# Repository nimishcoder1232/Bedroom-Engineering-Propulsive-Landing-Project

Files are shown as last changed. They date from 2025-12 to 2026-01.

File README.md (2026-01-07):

# Bedroom-Engineering-Propulsive-Landing-Project
This repo has everything that I made for my rocket that can propulsive landing, while still being under ITAR restrictions. 

For this project, I will design a rocket that can launch and then do a propulsive landing. In order to meet this challenge, I will have to make a new custom ESP32-based flight computer. I will have to make a quaternion orientation calculation system, I will have to design a control loop, and I will have to make a simulator in Python, without vibe coding, because it is too complicated. The simulator will simulate the rocket’s flight to help tune the control loop and the propulsive landing.

I did this project for a few reasons. The first reason I did it, is because in gneral, this is my passion. I love both engineering and rockets, so this is satisfactory for me. This isant a project for me, this project is more, who I am. I also made this project to learn from it. Throughout this project, I have learned sooo much, PCB design, CAD, Programign in many languages, soldering. And SO much more. Every time I sit down to do one of these projects, I end up learning so much. That is the second reason I work on these projects, To learn From them. 

Notes:
I am 3d printing everything myself, I DONT need reinbursment

The cad has all the parts. The engine, and the dc motor, and the syringes, are provided by me. 

The cad is ONE zip file. Once you unpack it, it has ALL the parts. the file in ALL CAPS called FULL ASEMBLY is the completed asembbly. 

No explosives are in any of the BOM, no engines, nothing. 

Project Link: https://blueprint.hackclub.com/projects/7459

Full Rocket: 



PCB schematic: 



PCB Routing: 



PCB Preview: 



Wiring Diagram: 

Any bold line is a electrical wire. I have color coded it. black for ground, red for power, and blue for saignals. if two same color lines touch, thats a connection, if two ddifferent colored lines overlaped, thats NOT a connection. 


|Item Name |Link |Quanity|Cost  USD|Notes |
|---|---|---|---|---|
|Carbon Fiber Rod 500mm 5 pack |https://www.aliexpress.com/item/3256806607506929.html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 |2 |9 | |
|drv8833 motor controler 1 pack |https://www.aliexpress.com/item/3256809542138701.html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 |1 |5 | |
|ES08MA &#124;&#124; servos 2 poack |https://www.aliexpress.com/item/3256809559338882.html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|1 |15 | |
|Solder Paste |https://www.aliexpress.com/item/3256804805080766.html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 |1 |7.11 | |
|Taxes deducted from Ali Express |N.A. |1 |4 | |
| | | | | |
|USB4105-GF-A |https://www.digikey.com/en/products/detail/gct/USB4105-GF-A/11198441 |2 |1.56 |Some of these components, I ordered extra because its LITTERLY cheaper to buy more|
|CP2102N-A02-GQFN28R |https://www.digikey.com/en/products/detail/silicon-labs/CP2102N-A02-GQFN28R/9863480 |2 |8.64 | |
|BMI270 |https://www.digikey.com/en/products/detail/bosch-sensortec/BMI270/9974486 |2 |7.46 | |
|BMP390 |https://www.digikey.com/en/products/detail/bosch-sensortec/BMP390/16164575 |2 |6.3 | |
|MMBT4401_R1_00001 |https://www.digikey.com/en/products/detail/panjit-international-inc/MMBT4401-R1-00001/14661149 |4 |0.64 | |
|OSTTE020104 |https://www.digikey.com/en/products/detail/on-shore-technology-inc/OSTTE020104/2351816 |10 |3.61 | |
|PS1240P02BT |https://www.digikey.com/en/products/detail/tdk-corporation/PS1240P02BT/935924 |2 |1.24 | |
|CL21B106KOQNNNE |https://www.digikey.com/en/products/detail/samsung-electro-mechanics/CL21B106KOQNNNE/3888530 |15 |0.53 | |
|C0805C104K5RACTU |https://www.digikey.com/en/products/detail/kemet/C0805C104K5RACTU/411169 |20 |0.32 | |
|B320A-13-F |https://www.digikey.com/en/products/detail/diodes-incorporated/B320A-13-F/717692 |6 |1.56 | |
|ESD5Z5.0T5G |https://www.digikey.com/en/products/detail/onsemi/ESD5Z5-0T5G/5404303 |10 |0.99 | |
|TPS565208DDCR |https://www.digikey.com/en/products/detail/texas-instruments/TPS565208DDCR/7776393 |2 |2.76 | |
|LD1117S33TR |https://www.digikey.com/en/products/detail/stmicroelectronics/LD1117S33TR/585766 |2 |0.68 | |
|ESP32-S3-WROOM-1-N8 |https://www.digikey.com/en/products/detail/espressif-systems/ESP32-S3-WROOM-1-N8/15200089 |2 |10.98 | |
|CL21B105KBFNNNE |https://www.digikey.com/en/products/detail/samsung-electro-mechanics/CL21B105KBFNNNE/3886687 |10 |0.13 | |
|CL21A226MAYNNNE |https://www.digikey.com/en/products/detail/samsung-electro-mechanics/CL21A226MAYNNNE/10479857 |3 |0.24 | |
|LTST-C170GKT |https://www.digikey.com/en/products/detail/liteon/LTST-C170GKT/269226 |3 |0.3 | |
|AO3400A |https://www.digikey.com/en/products/detail/alpha-omega-semiconductor-inc/AO3400A/1855772 |10 |2.82 | |
|MLZ2012P220WT000 |https://www.digikey.com/en/products/detail/tdk-corporation/MLZ2012P220WT000/4327893 |2 |0.2 | |
|CRCW08051K00FKEA |https://www.digikey.com/en/products/detail/vishay-dale/CRCW08051K00FKEA/1175637 |2 |0.2 | |
|RMCF0805FT22K1 |https://www.digikey.com/en/products/detail/stackpole-electronics-inc/RMCF0805FT22K1/1760211 |10 |0.07 | |
|RMCF0805FT10K0 |https://www.digikey.com/en/products/detail/stackpole-electronics-inc/RMCF0805FT10K0/1760676 |16 |0.21 | |
|RC0805JR-075K1L |https://www.digikey.com/en/products/detail/yageo/RC0805JR-075K1L/728338 |10 |0.08 | |
|W25Q128JVSIM |https://www.digikey.com/en/products/detail/winbond-electronics/W25Q128JVSIM/6819721 |2 |3.94 | |
|RC0805FR-072K2L |https://www.digikey.com/en/products/detail/yageo/RC0805FR-072K2L/727676 |10 |0.1 | |
|RC0805FR-0747K5L |https://www.digikey.com/en/products/detail/yageo/RC0805FR-0747K5L/727975 |10 |0.1 | |
|RT0805BRD0759R7L |https://www.digikey.com/en/products/detail/yageo/RT0805BRD0759R7L/7708567 |2 |0.32 | |
|RC0805FR-07330RL |https://www.digikey.com/en/products/detail/yageo/RC0805FR-07330RL/727866 |10 |0.1 | |
|Dijikey Shipping |N.A. |1 |7 | |
|Sales tax + terrifs (Dijikey) |N.A. |1 |8 | |
| | | | | |
|JLCPCB 4 Layer PCB + stencil + Global Standard Dirrect Line + sales tax|JLC PCB |5 |33 | |
| | | | | |
|JLC PCB order |33 | | | |
| | | | | |
|Ali express order |40.11 | | | |
| | | | | |
|Dijikey Order |71.08 | | | |
| | | | | |
|Total Cost |144.19 | | | |

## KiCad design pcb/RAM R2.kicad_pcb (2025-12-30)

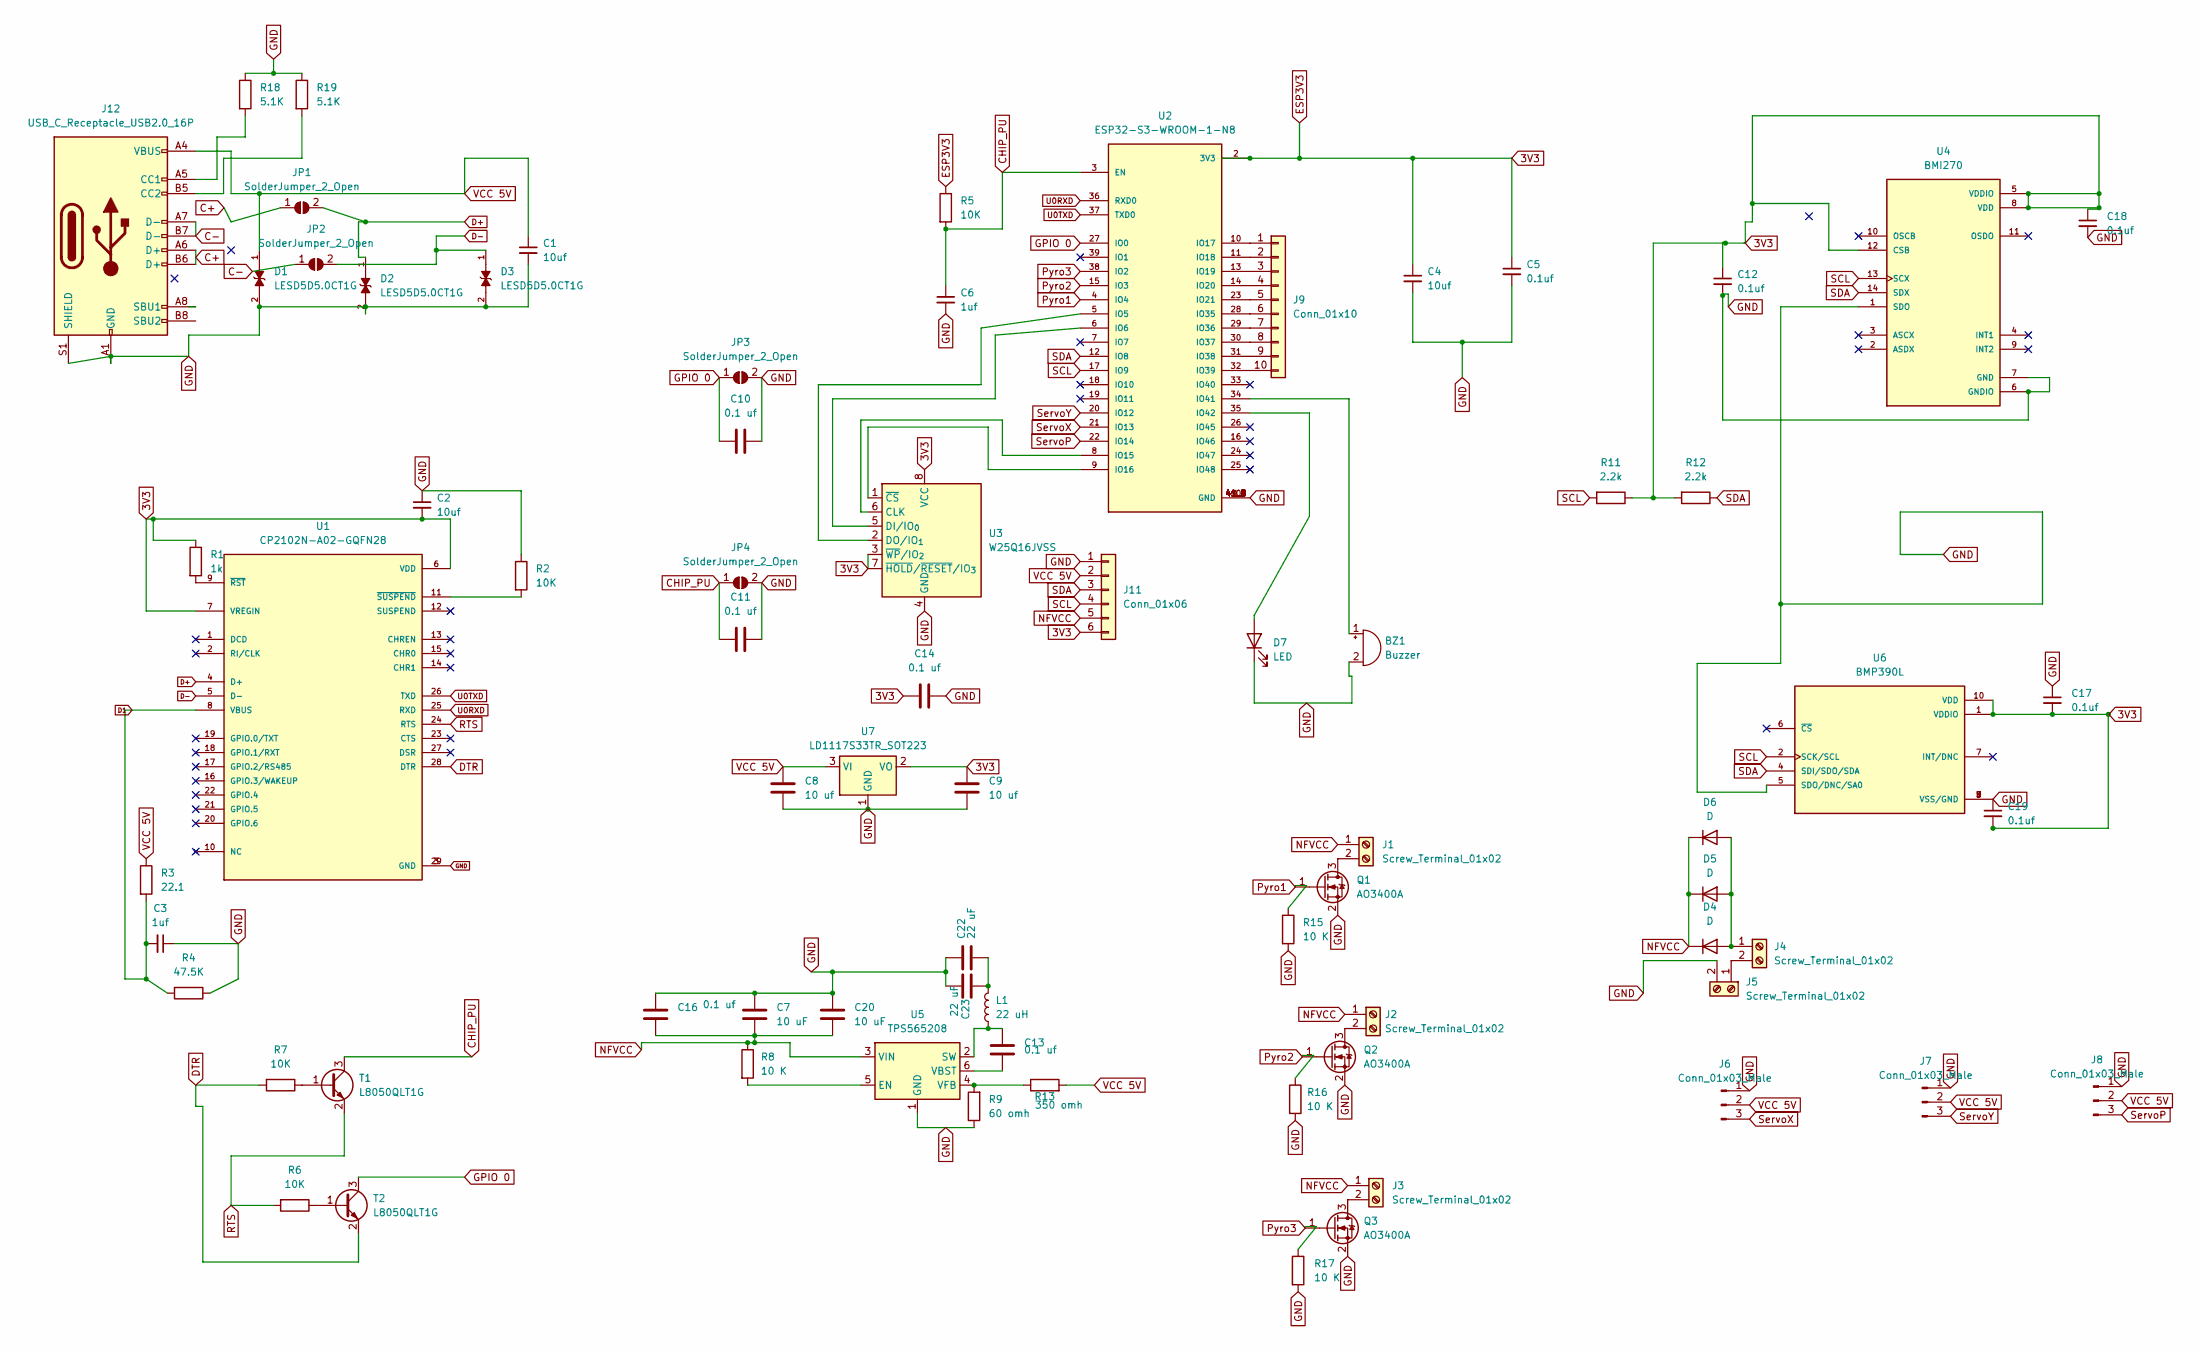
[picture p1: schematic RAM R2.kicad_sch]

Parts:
BZ1: Buzzer; Buzzer_TDK_PS1240P02BT_D12.2mm_H6.5mm
C1, C2, C4: 10uf; C_0805_2012Metric
C3, C6: 1uf; C_0805_2012Metric
C5, C12, C17, C18, C19: 0.1uf; C_0805_2012Metric
C7, C20: 10 uF; C_0805_2012Metric
C8, C9: 10 uf; C_0805_2012Metric
C10, C11, C13, C14, C16: 0.1 uf; C_0805_2012Metric
C22, C23: 22 uF; C_0805_2012Metric
D1, D2, D3: LESD5D5.0CT1G; TVS_LESD5D5.0CT1G; PARTREV O
D4, D5, D6: D; D_SMA
D7: LED; LED_0805_2012Metric
J1, J2, J3, J4, J5: Screw_Terminal_01x02; TerminalBlock_4Ucon_1x02_P3.50mm_Horizontal
J6, J7, J8: Conn_01x03_Male; PinHeader_1x03_P2.54mm_Vertical
J9: Conn_01x10; 10 pad genaric
J11: Conn_01x06; 6pad genaric
J12: USB_C_Receptacle_USB2.0_16P; USB_C_Receptacle_GCT_USB4105-xx-A_16P_TopMnt_Horizontal
JP1, JP2, JP3, JP4: SolderJumper_2_Open; SolderJumper-2_P1.3mm_Open_Pad1.0x1.5mm
L1: 22 uH; L_0805_2012Metric
Q1, Q2, Q3: AO3400A; SOT-23
R1: 1k; R_0805_2012Metric
R2, R5, R6, R7: 10K; R_0805_2012Metric
R3: 22.1; R_0805_2012Metric
R4: 47.5K; R_0805_2012Metric
R8, R15, R16, R17: 10 K; R_0805_2012Metric
R9: 60 omh; R_0805_2012Metric
R11, R12: 2.2k; R_0805_2012Metric
R13: 350 omh; R_0805_2012Metric
R18, R19: 5.1K; R_0805_2012Metric
T1, T2: L8050QLT1G; SOT-23
U1: CP2102N-A02-GQFN28; QFN50P500X500X80-29N; PARTREV 1.5
U2: ESP32-S3-WROOM-1-N8; XCVR_ESP32-S3-WROOM-1-N8
U3: W25Q16JVSS; SOIC-8_5.3x5.3mm_P1.27mm
U4: BMI270; XDCR_BMI270
U5: TPS565208; SOT-23-6
U6: BMP390L; XDCR_BMP390L; PARTREV 1.7
U7: LD1117S33TR_SOT223; SOT-223-3_TabPin2

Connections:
3V3: C2.2, C4.1, C5.1, C9.1, C12.1, C14.2, C17.2, C18.1, C19.2, J11.6, R1.1, R5.1, R11.1, R12.2, U1.6 (VDD), U1.7 (VREGIN), U2.2 (3V3), U3.3 (~WP/IO_{2}), U3.7 (~HOLD/~RESET/IO_{3}), U3.8 (VCC), U4.5 (VDDIO), U4.8 (VDD), U4.12 (CSB), U6.1 (VDDIO), U6.10 (VDD), U7.2 (VO)
C+: J12.A6 (D+), J12.B6 (D+), JP1.1 (A)
C-: J12.A7 (D-), J12.B7 (D-), JP2.1 (A)
CHIP_PU: C6.1, C11.2, JP4.1 (A), R5.2, T1.3 (C), U2.3 (EN)
D1: C3.2, R3.2, R4.2, U1.8 (VBUS)
D+: D2.1, JP1.2 (B), U1.4 (D+)
D-: D3.1, JP2.2 (B), U1.5 (D-)
DTR: R7.2, T2.2 (E), U1.28 (DTR)
GND: BZ1.2 (+), C1.2, C2.1, C3.1, C4.2, C5.2, C6.2, C7.1, C8.2, C9.2, C10.1, C11.1, C12.2, C14.1, C16.1, C17.1, C18.2, C19.1, C20.1, C22.1, C23.1, D1.2, D2.2, D3.2, D7.1 (K), J5.2, J6.1, J7.1, J8.1, J11.1, J12.A1 (GND), J12.A12 (GND), J12.B1 (GND), J12.B12 (GND), J12.S1 (SHIELD), JP3.2 (B), JP4.2 (B), Q1.2 (S), Q2.2 (S), Q3.2 (S), R2.1, R4.1, R9.1, R15.2, R16.2, R17.2, R18.1, R19.1, U1.3 (GND), U1.29 (GND), U2.1 (GND), U2.40 (GND), U2.41_1 (GND), U2.41_2 (GND), U2.41_3 (GND), U2.41_4 (GND), U2.41_5 (GND), U2.41_6 (GND), U2.41_7 (GND), U2.41_8 (GND), U2.41_9 (GND), U3.4 (GND), U4.1 (SDO), U4.6 (GNDIO), U4.7 (GND), U5.1 (GND), U6.3 (VSS/GND), U6.5 (SDO/DNC/SA0), U6.8 (VSS/GND), U6.9 (VSS/GND), U7.1 (GND)
GPIO 0: C10.2, JP3.1 (A), T2.3 (C), U2.27 (IO0)
NFVCC: C7.2, C16.2, C20.2, D4.1 (K), D5.1 (K), D6.1 (K), J1.1, J2.1, J3.1, J11.5, R8.1, U5.3 (VIN)
unnamed: BZ1.1 (-), U2.34 (IO41)
unnamed: C22.2, C23.2, L1.2
unnamed: D4.2 (A), D5.2 (A), D6.2 (A), J4.1
unnamed: D7.2 (A), U2.35 (IO42)
unnamed: J1.2, Q1.3 (D)
unnamed: J2.2, Q2.3 (D)
unnamed: J3.2, Q3.3 (D)
unnamed: J4.2, J5.1
unnamed: J9.1, U2.10 (IO17)
unnamed: J9.2, U2.11 (IO18)
unnamed: J9.3, U2.13 (IO19)
unnamed: J9.4, U2.14 (IO20)
unnamed: J9.5, U2.23 (IO21)
unnamed: J9.6, U2.28 (IO35)
unnamed: J9.7, U2.29 (IO36)
unnamed: J9.8, U2.30 (IO37)
unnamed: J9.9, U2.31 (IO38)
unnamed: J9.10, U2.32 (IO39)
unnamed: J12.A5 (CC1), R18.2
unnamed: J12.B5 (CC2), R19.2
unnamed: R7.1, T1.1 (B)
unnamed: R6.1, T2.1 (B)
unnamed: R1.2, U1.9 (~RST)
unnamed: R2.2, U1.11 (~SUSPEND)
unnamed: U2.5 (IO5), U3.2 (DO/IO_{1})
unnamed: U2.6 (IO6), U3.5 (DI/IO_{0})
unnamed: U2.8 (IO15), U3.6 (CLK)
unnamed: U2.9 (IO16), U3.1 (~CS)
unnamed: R8.2, U5.5 (EN)
unnamed: C13.1, L1.1, U5.2 (SW)
unnamed: C13.2, U5.6 (VBST)
unnamed: R9.2, R13.1, U5.4 (VFB)
Pyro1: Q1.1 (G), R15.1, U2.4 (IO4)
Pyro2: Q2.1 (G), R16.1, U2.15 (IO3)
Pyro3: Q3.1 (G), R17.1, U2.38 (IO2)
RTS: R6.2, T1.2 (E), U1.24 (RTS)
SCL: J11.4, R11.2, U2.17 (IO9), U4.13 (SCX), U6.2 (SCK/SCL)
SDA: J11.3, R12.1, U2.12 (IO8), U4.14 (SDX), U6.4 (SDI/SDO/SDA)
ServoP: J8.3, U2.22 (IO14)
ServoX: J6.3, U2.21 (IO13)
ServoY: J7.3, U2.20 (IO12)
U0RXD: U1.25 (RXD), U2.36 (RXD0)
U0TXD: U1.26 (TXD), U2.37 (TXD0)
VCC 5V: C1.1, C8.1, D1.1, J6.2, J7.2, J8.2, J11.2, J12.A4 (VBUS), J12.A9 (VBUS), J12.B4 (VBUS), J12.B9 (VBUS), R3.1, R13.2, U7.3 (VI)

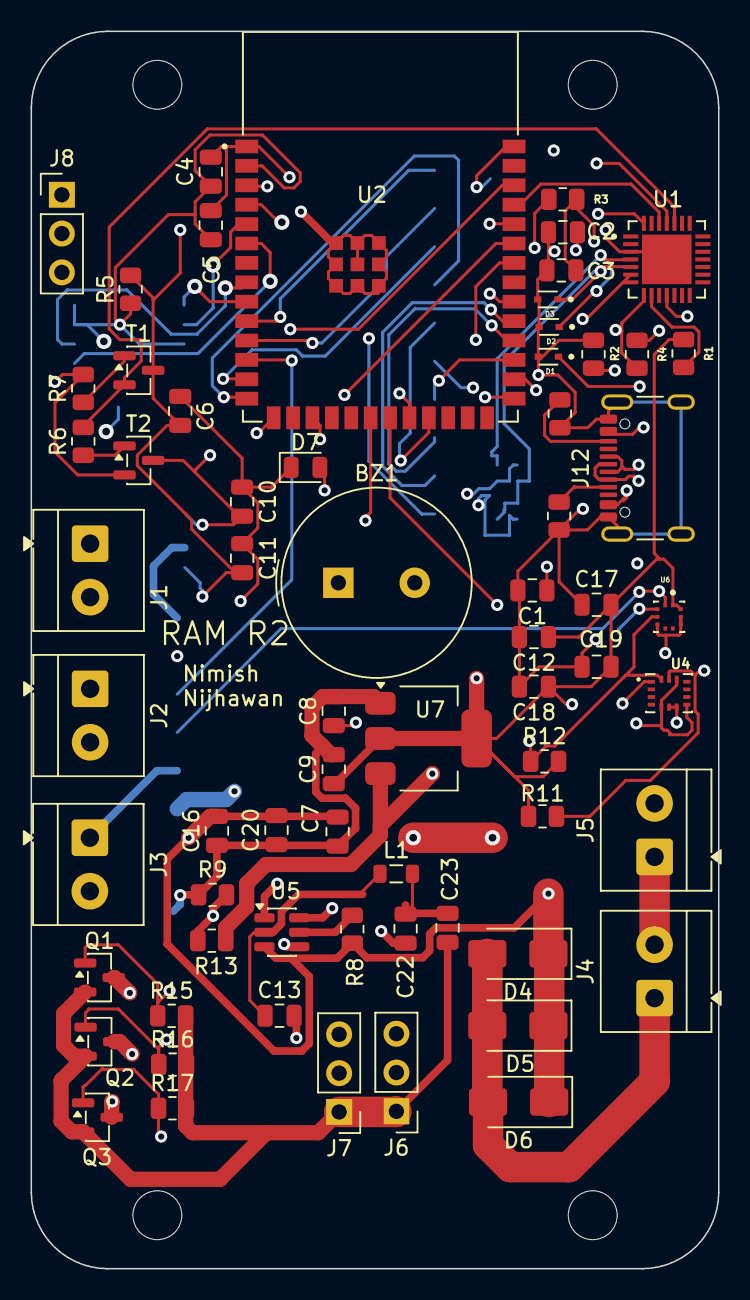
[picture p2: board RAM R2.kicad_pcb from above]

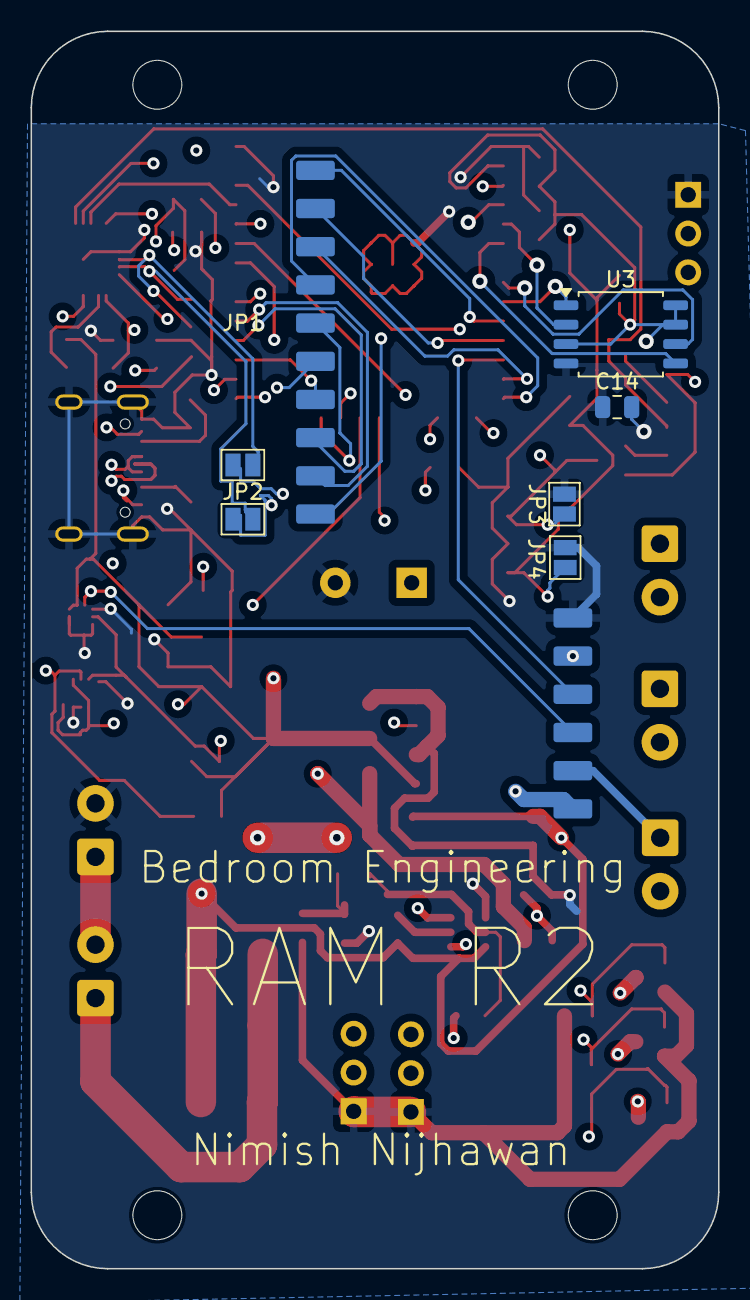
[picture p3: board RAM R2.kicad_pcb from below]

Board: 4 copper layers, 45.0 x 81.0 mm, 74 parts (8 on the bottom side), 55 nets.

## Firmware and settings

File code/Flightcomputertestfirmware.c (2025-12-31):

/*
This code tests the flight computer, and all of its functions, and proves capibilites liek PID. it DOES NOT have actual rocket guidence code, since that is ileagal.
A blueprint organizer has aproved, that I dont have to provide the guidence code in github. The real code DOES exist, but I cant share it.
*/

#include <Wire.h>
#include <ESP32Servo.h>
#include <Adafruit_BMP3XX.h>
#include "BMI270_SensorAPI.h"

// ================= PINS =================
#define SERVO_PIN 25
#define PYRO1_PIN 26
#define PYRO2_PIN 27

// ================= OBJECTS =================
Servo testServo;
Adafruit_BMP3XX bmp;

// BMI270 variables
struct bmi2_dev bmi;
struct bmi2_sens_data sensor_data;

// ================= PID =================
float targetAngle = 0.0;   // degrees
float angle = 0.0;
float gyroRate = 0.0;

float Kp = 3.0;
float Ki = 0.02;
float Kd = 0.15;

float error, lastError = 0;
float integral = 0;
float derivative;
float pidOutput;

// Timing
unsigned long lastTime;

// ================= BMI CALLBACKS =================
int8_t bmi_read(uint8_t reg, uint8_t *data, uint32_t len, void *intf_ptr) {
  Wire.beginTransmission(BMI2_I2C_PRIM_ADDR);
  Wire.write(reg);
  Wire.endTransmission(false);
  Wire.requestFrom(BMI2_I2C_PRIM_ADDR, len);
  for (uint32_t i = 0; i < len; i++) data[i] = Wire.read();
  return BMI2_OK;
}

int8_t bmi_write(uint8_t reg, const uint8_t *data, uint32_t len, void *intf_ptr) {
  Wire.beginTransmission(BMI2_I2C_PRIM_ADDR);
  Wire.write(reg);
  for (uint32_t i = 0; i < len; i++) Wire.write(data[i]);
  Wire.endTransmission();
  return BMI2_OK;
}

void bmi_delay(uint32_t ms, void *intf_ptr) {
  delay(ms);
}

// ================= SETUP =================
void setup() {
  Serial.begin(115200);
  Wire.begin();

  pinMode(PYRO1_PIN, OUTPUT);
  pinMode(PYRO2_PIN, OUTPUT);
  digitalWrite(PYRO1_PIN, LOW);
  digitalWrite(PYRO2_PIN, LOW);

  // Servo
  testServo.setPeriodHertz(50);
  testServo.attach(SERVO_PIN, 1000, 2000);

  // BMP390
  if (!bmp.begin_I2C()) {
    Serial.println("BMP390 FAIL");
    while (1);
  }

  bmp.setTemperatureOversampling(BMP3_OVERSAMPLING_8X);
  bmp.setPressureOversampling(BMP3_OVERSAMPLING_4X);
  bmp.setIIRFilterCoeff(BMP3_IIR_FILTER_COEFF_3);

  // BMI270
  bmi.intf = BMI2_I2C_INTF;
  bmi.read = bmi_read;
  bmi.write = bmi_write;
  bmi.delay_us = bmi_delay;
  bmi.intf_ptr = NULL;

  if (bmi270_init(&bmi) != BMI2_OK) {
    Serial.println("BMI270 FAIL");
    while (1);
  }

  bmi2_sens_config config[2];
  config[0].type = BMI2_ACCEL;
  config[1].type = BMI2_GYRO;

  bmi2_set_sensor_config(config, 2, &bmi);
  bmi2_sensor_enable(BMI2_ACCEL | BMI2_GYRO, &bmi);

  lastTime = millis();

  Serial.println("SYSTEM OK");
}

// ================= LOOP =================
void loop() {
  unsigned long now = millis();
  float dt = (now - lastTime) / 1000.0;
  lastTime = now;

  // ===== IMU =====
  bmi2_get_sensor_data(&sensor_data, &bmi);

  float ax = sensor_data.acc.x / 16384.0;
  float az = sensor_data.acc.z / 16384.0;
  gyroRate = sensor_data.gyr.y * 0.061; // deg/s

  float accelAngle = atan2(ax, az) * 57.2958;

  // Complementary filter
  angle = 0.98 * (angle + gyroRate * dt) + 0.02 * accelAngle;

  // ===== PID =====
  error = targetAngle - angle;
  integral += error * dt;
  derivative = (error - lastError) / dt;
  lastError = error;

  pidOutput = Kp * error + Ki * integral + Kd * derivative;
  pidOutput = constrain(pidOutput, -30, 30);

  // Servo center = 90
  testServo.write(90 + pidOutput);

  // ===== BARO =====
  bmp.performReading();

  // ===== PYRO TEST (VERY SHORT PULSE) =====
  static unsigned long lastPyro = 0;
  if (millis() - lastPyro > 5000) {
    digitalWrite(PYRO1_PIN, HIGH);
    delay(50);
    digitalWrite(PYRO1_PIN, LOW);
    lastPyro = millis();
  }

  // ===== DEBUG =====
  Serial.print("Angle:");
  Serial.print(angle);
  Serial.print(" PID:");
  Serial.print(pidOutput);
  Serial.print(" Alt:");
  Serial.println(bmp.readAltitude(1013.25));

  delay(10);
}

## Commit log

2025-12-30 Rename RAM R2.kicad_pcb to pcb/RAM R2.kicad_pcb
    [RAM R2.kicad_pcb]
2025-12-30 Rename RAM R2.kicad_prl to pcb/RAM R2.kicad_prl
2025-12-30 Rename RAM R2.kicad_pro to pcb/RAM R2.kicad_pro
2025-12-31 Rename RAM R2.kicad_sch to pcb/RAM R2.kicad_sch
    [RAM R2.kicad_sch]
2025-12-31 Add rocket flight simulation with PID tuning
    This program simulates a rocket's flight characteristics and allows tuning of PID variables. It includes physics constants and implements thrust calculations based on gimbal angles.
2025-12-31 Improve comments and fix spelling in flight computer test
    Updated comments for clarity and corrected spelling errors.
    [Flightcomputertestfirmware.c]
2025-12-31 Rename full asembly.step to cad/full asembly.step
    [full asembly.step]
2025-12-31 Update and rename Rocket BOM - Sheet1.csv to BOM.csv
    [BOM.csv]
2025-12-31 Update and rename BOM - Sheet1.csv to BOM .csv
    [BOM .csv]
2025-12-31 Update and rename BOM .csv to BOM.csv
    [BOM.csv]
2026-01-02 Update and rename BOM - Sheet1 (1).csv to BOM.csv
    [BOM.csv]
2026-01-05 Fix typo in BOM description in README.md
2026-01-05 Enhance README with wiring diagram and details
    Added wiring diagram and explanation to README.
